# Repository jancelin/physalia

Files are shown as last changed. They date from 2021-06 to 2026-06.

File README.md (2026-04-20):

# PHYSALIA

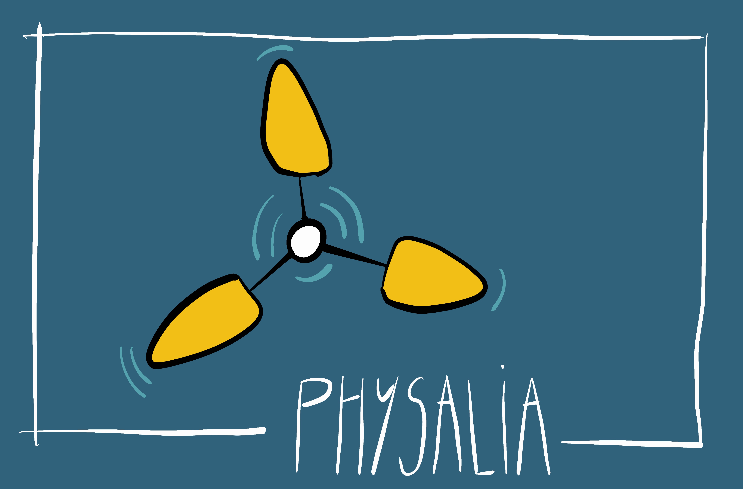
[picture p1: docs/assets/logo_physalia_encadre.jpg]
Physalia


## Plateforme HYdrographique pour la Surveillance Altimétrique du LIttoral

La surveillance du niveau de la mer et des niveaux hydrauliques des marais est un enjeu majeur dans la compréhension des dynamiques côtières et hydrologiques. Plusieurs études ont montré l’efficacité des bouées GNSS appliquées à la mesure du niveau de la mer. Toutefois, leur usage est généralement limité par le coût élevé d’un tel dispositif.

Plusieurs prototypes de bouées GNSS-RTK ont été développés afin de répondre à des problématiques liées à la surveillance en temps réel des variations du niveau de la mer et des marais littoraux. La réalisation des bouées est caractérisée par un besoin de réduction importante des coûts pour les rendre accessibles à tous.
Les bouées ont été construites autour d’une structure centrale et sont équipées de trois flotteurs montés sur des bras en acier inoxydable. La réception des signaux GNSS est assurée par un récepteur tri-fréquences qui utilise les constellations GPS, GLONASS, Galileo et Beidou. Les corrections RTK sont obtenues par le réseau [CentipedeRTK](https://centipede-rtk.org/). La réception des correction et le transfert des données produites est assurée par une connexion LTE.

## Objectifs

L’objectif et de suivre en continue avec une précision centimétrique les niveaux d’eau sur différents sites expérimentaux en marais doux atlantiques.

partenaires

-------------------------------------------------------
# Versions

## Physalia V1 maritime

version1

## Physalita hydro Marais

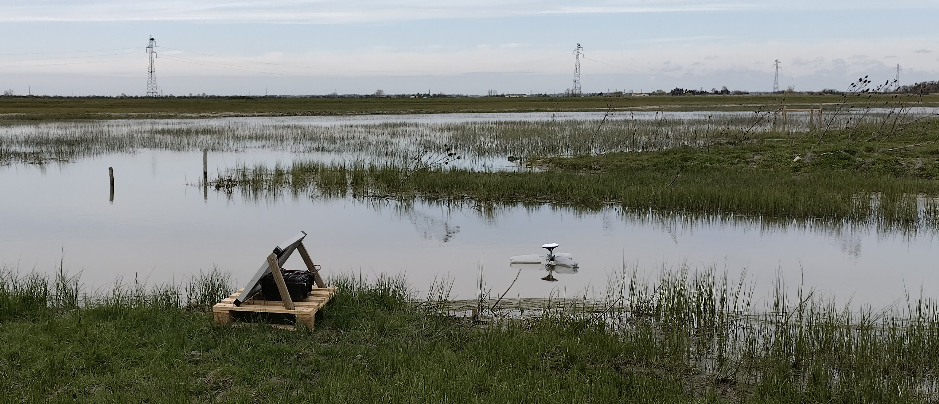
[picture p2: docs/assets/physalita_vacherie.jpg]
version_physalita


## Physalia V2 en développement

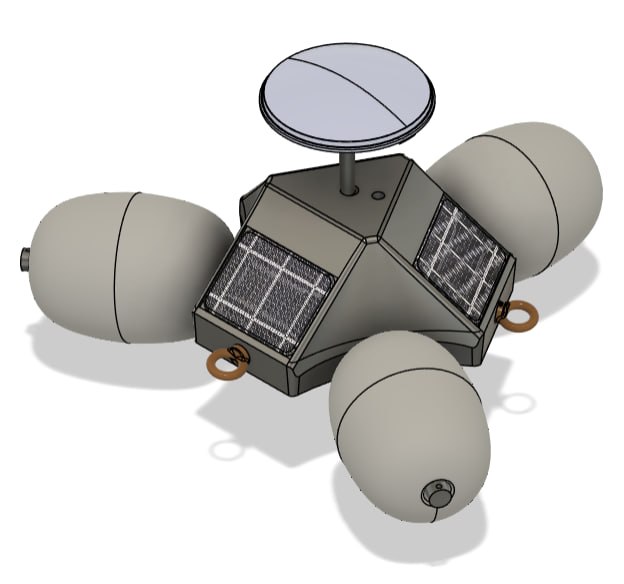
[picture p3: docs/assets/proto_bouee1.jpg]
version2


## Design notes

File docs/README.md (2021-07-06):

---
layout: default
title: 404
nav_exclude: true
---

# PHYSALIA

Documentation de PHYSALIA

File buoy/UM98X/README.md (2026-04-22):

# CONFIGURATION UM980

* Avec le navigateur Chrome ou Edge ouvrir la page https://webserial.centipede.fr/index_advanced.html
* connecter en USB le ROVER
* cliquer sur *Connecter*
* Uploader le fichier de configuration *UM90.cfg*
* cliquer sur *Envoyer*

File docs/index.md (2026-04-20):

---
layout: default
title: PHYSALIA
nav_order: 1
has_children: true
---

# PHYSALIA

Physalia

## Plateforme HYdrographique pour la Surveillance Altimétrique du LIttoral

La surveillance du niveau de la mer et des niveaux hydrauliques des marais est un enjeu majeur dans la compréhension des dynamiques côtières et hydrologiques. Plusieurs études ont montré l’efficacité des bouées GNSS appliquées à la mesure du niveau de la mer. Toutefois, leur usage est généralement limité par le coût élevé d’un tel dispositif.

Plusieurs prototypes de bouées GNSS-RTK ont été développés afin de répondre à des problématiques liées à la surveillance en temps réel des variations du niveau de la mer et des marais littoraux. La réalisation des bouées est caractérisée par un besoin de réduction importante des coûts pour les rendre accessibles à tous.
Les bouées ont été construites autour d’une structure centrale et sont équipées de trois flotteurs montés sur des bras en acier inoxydable. La réception des signaux GNSS est assurée par un récepteur tri-fréquences qui utilise les constellations GPS, GLONASS, Galileo et Beidou. Les corrections RTK sont obtenues par le réseau de base, [CentipedeRTK](https://centipede-rtk.org/). La réception des correction et le transfert des données produites est assurée par une connexion LTE.

## Objectifs

L’objectif et de suivre en continue avec une précision centimétrique les niveaux d’eau sur différents sites expérimentaux en marais doux atlantiques.

partenaires

-------------------------------------------------------
# Versions

## Physalia V1 maritime

version1

## Physalita hydro Marais

version_physalita

## Physalia V2 en développement

version2

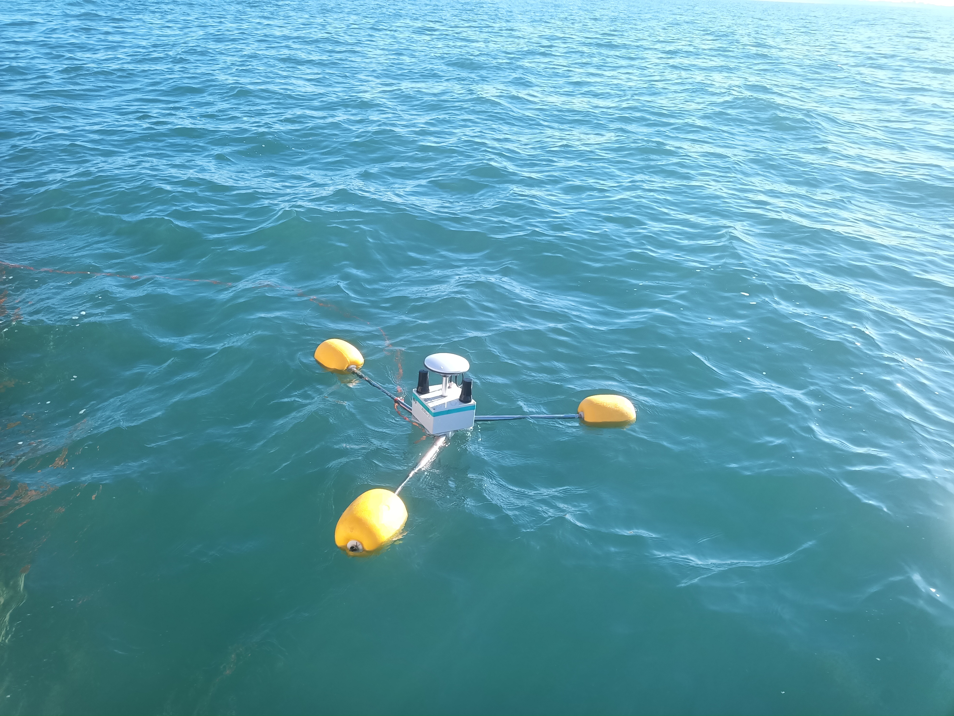
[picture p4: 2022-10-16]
docs/assets/thalia1_1022.jpg

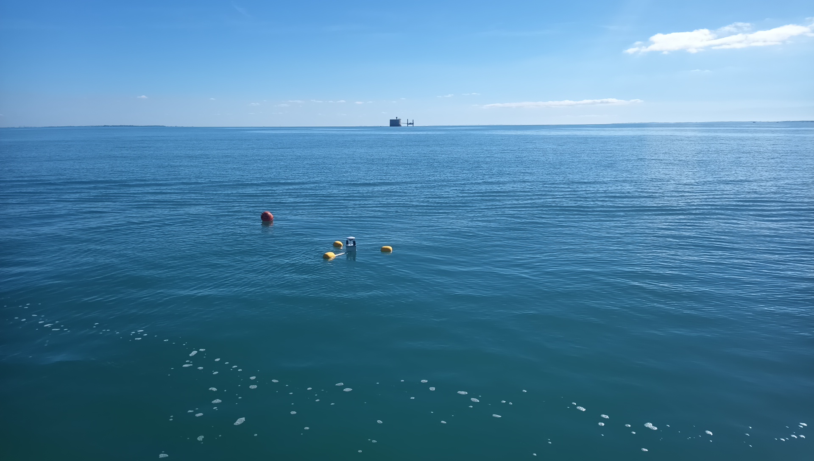
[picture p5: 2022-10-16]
docs/assets/thalia2_1022.jpg

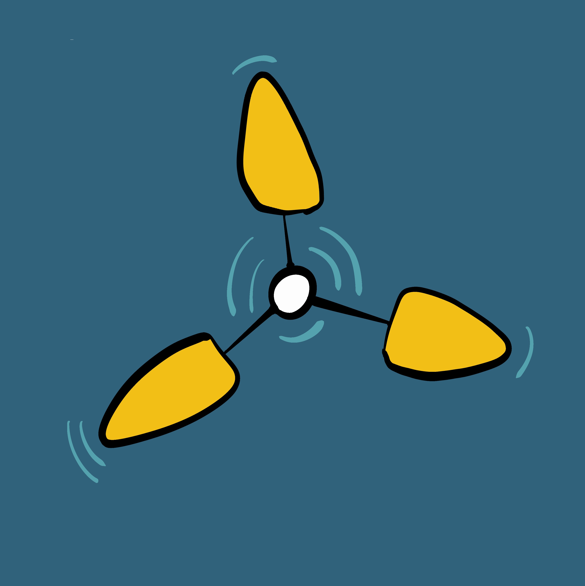
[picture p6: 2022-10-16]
docs/assets/logo.jpg

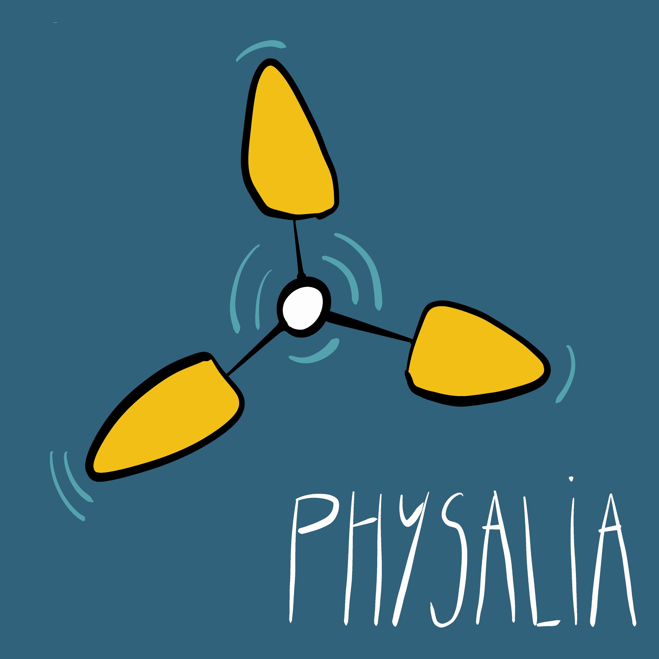
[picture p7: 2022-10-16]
docs/assets/logo_physalia.jpg

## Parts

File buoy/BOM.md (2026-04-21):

# BOM

## Elecronique

| composant | lien | Qte | prix unitaire HT |
| --- | --- | --- | --- |
| Mallette de transport Peli 1020 | https://fr.rs-online.com/web/p/mallettes-de-transport/0618786?gb=a | 1 | 31.4€ |
| Presse-étoupe HSK-K, M16 Hummel Gris, en Polyamide, IP68, Ø 4 mm à Ø 8 mm | https://fr.rs-online.com/web/p/presse-etoupes/0340144 | 1 | 0.44€ |
| diodes Schottky 1N5819 | https://fr.rs-online.com/web/p/diodes-schottky-et-de-redressements/4864460 | 3 | 0.94€ |
| Solar Panel 5V 200mA 110×80 mm | https://www.tinytronics.nl/en/power/solar-energy/solar-panels/solar-panel-5v-200ma-110x80mm | 3 | 3.5€ |
| Molicel 18650 Li-ion Battery - 3500mAh - 10A - INR18650-M35A | https://www.tinytronics.nl/en/power/batteries/18650/molicel-18650-li-ion-battery-3500mah-10a-inr18650-m35a | 1 | 4.13€ |
| LilyGO T-SIM7600G-H R2 - ESP32-WROVER - with 18650 Battery Holder | https://www.tinytronics.nl/en/development-boards/microcontroller-boards/with-telecommunication/lilygo-ttgo-t-sim7600g-h-r2-esp32-wrover-with-18650-battery-holder | 1 | 53.31€ |
| USB-C 2.0 Female to DIP Adapter | https://www.tinytronics.nl/en/cables-and-connectors/connectors/usb/usb-c-2.0-female-to-dip-adapter | 1 | 0.74€ |
| Pololu Mini interrupteur à glissière MOSFET avec protection contre les inversions de tension, LV | https://opencircuit.fr/produit/mini-mosfet-slide-switch-reverse-voltage | 1 | 3.4€ |
| UM980 Mic RTK GNSS receiver | https://gnss.store/products/elt0224 | 1 | 160€ |
| Budget All-band high precision GNSS antenna | https://gnss.store/products/elt0323 | 1 | 130€ |
| IP65 IPEX (U.FL) to SMA cable lenght 100mm panel thickness 8mm | http://gnss.store/products/elt0179?variant=55851776344396 | 1 | 6€ |
| Cordon sur mesure en coax faible perte UltraFlex LMR-240-UF 2.4/5 GHz (Ø 6.1mm) SMA mâle > TNC mâle 30 cm (sur demande) | http://mhzshop.com/Cables-et-cordons/Sur-mesure/50-ohms-WiFi-4G/Cordon-sur-mesure-en-coax-faible-perte-UltraFlex-LMR-240-UF-2-4-5-GHz-O-6-1mm.html | 1 | 19.6€ |
| total |  | | 422.34€| 
| Adafruit Ensemble de bobines de fil de raccordement - noyau solide 22AWG - 6 x 25 pi | https://opencircuit.fr/produit/hook-up-wire-spool-set-22awg-solid-core-6-x-25 | 1 | 21.6€ |
|  |  | | | 
| total |  | | 444€| 

## Structure

| matériel | lien | Qte | prix unitaire HT |
| --- | --- | --- | --- |
| Flotteur PB600 630g flottabilité 97x150mm  trou de 20mm Ø  | https://engelnetze.com/fr/flotteur-pb600-630g-flottabilite-97x150mm-trou-de-20mm/ | 3 | 6.2€ |  !
| tube inox ou fibre de verre |  | | |  
| platine assemblage |  | | |  
| Beitian RTK GNSS Base d'antenne GPS BT-M110SLB 18cm | https://fr.aliexpress.com/item/1005008470759973.html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 | 1 | 24.4€ |  
| tige d'extension de connexion GPS RTK en Fiber de carbone noire, mesure d'arpentage, diamètre 32mm, 10cm | https://fr.aliexpress.com/item/1005008788295319.html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 | 1 | 4.69€ |

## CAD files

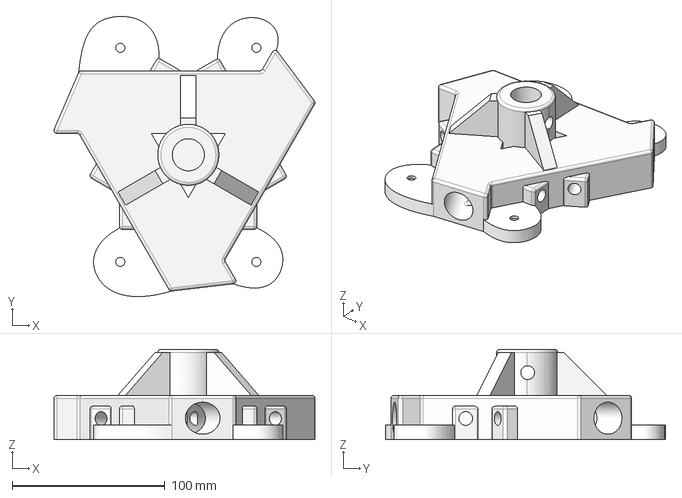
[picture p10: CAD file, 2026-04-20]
buoy/Printed-Parts/STEP/plan_corp_v1_8_4-Fusion041.step
170.7 x 183.3 x 59.0 mm

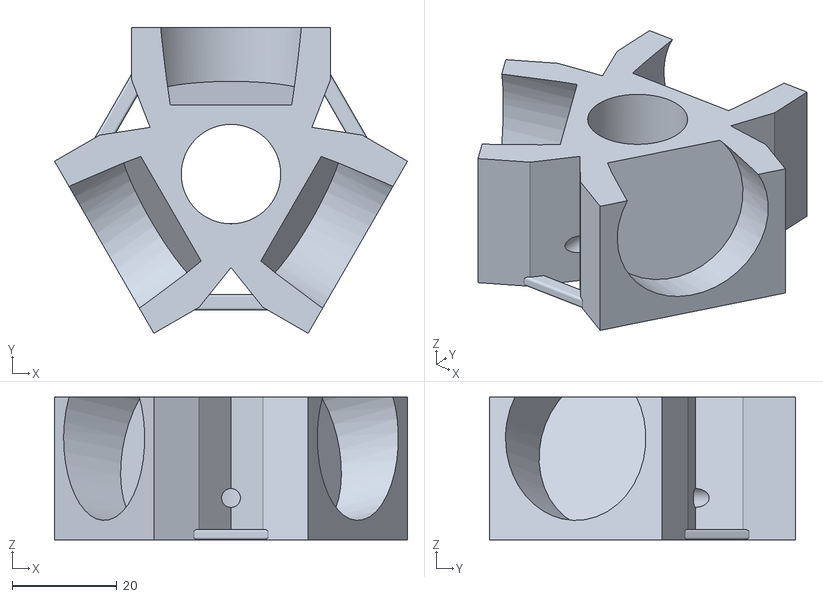
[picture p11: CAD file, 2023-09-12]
buoy/Printed-Parts/STL/physalita_5.stl
67.5 x 58.5 x 27.3

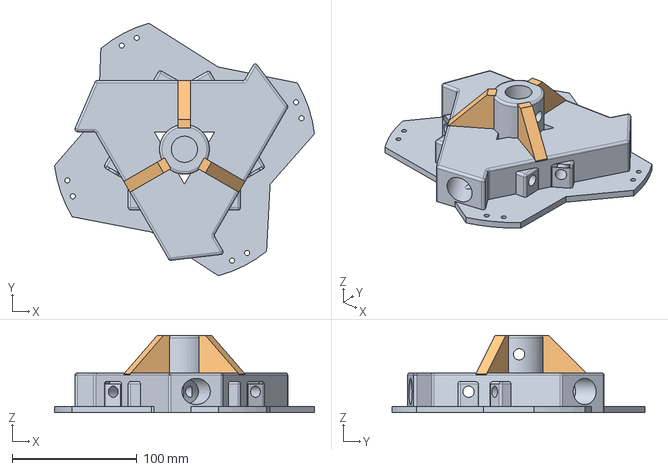
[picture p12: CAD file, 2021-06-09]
buoy/Printed-Parts/STEP/physalia_v1_7.step
208.4 x 202.5 x 62.0 mm

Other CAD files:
buoy/Printed-Parts/STL/physalia_v1_7.stl
buoy/Printed-Parts/STL/plan_corp_v1_8_4-Fusion041.stl
buoy/Printed-Parts/plan_corp_v1_8_4-Fusion041.3mf

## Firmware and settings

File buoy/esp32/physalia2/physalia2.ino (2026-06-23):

/*
=============================================================================================
PHYSALIA2 - UM980 edition
  - LTE NTRIP rover over SIM7600 (T-SIM7600G-H R2)
  - GNSS telemetry over MQTT
  - RTK fix via réseau Centipède-RTK (NTRIP)

Version énergie / mesure scientifique :
  Core 0 : gnssTask – lit l'UM980 en continu et pousse les PVTSLNA dans une queue courte.
  Core 1 : loop     – LTE/NTRIP/RTCM, stockage local des positions, publication MQTT groupée.
  
  Structure des fichiers :
  physalia2_dualcore.ino  – globals, setup(), loop(), gnssTask()
  ph_config.h             – pins, macros log, includes communs
  ph_globals.h            – struct PvtslnData + extern des globals
  ph_watchdog.cpp         – TWDT, failure handling, safeDeepSleep, BT off
  ph_modem.cpp            – setupGsm, maintainNetwork, modem_on/off, reset périodique
  ph_gnss.cpp             – processGnssSerial, parsePvtslnLine, setupGnss
  ph_ntrip.cpp            – maintainNtrip, processNtripStream, sendPeriodicGGA
  ph_mqtt.cpp             – publishFix, reconnect, callback, mapPositionType
  ph_battery.cpp          – ADC, readVbatMv, publishBatteryIfDue, publishPreSleepVbat
  ph_sleep.cpp            – setupDeepSleep, print_wakeup_reason
  secrets.h               – identifiants, paramètres réseau/timing
  secrets.cpp             – définitions uniques des variables globales
  NTRIPClient.h/.cpp      – librairie NTRIP
=============================================================================================
*/

#include "ph_config.h"
#include "ph_globals.h"
#include "secrets.h"

// =============================================================================
// DÉFINITIONS des objets et variables globales (extern déclarés dans ph_globals.h)
// =============================================================================

#ifdef DUMP_AT_COMMANDS
  #include <StreamDebugger.h>
  StreamDebugger _dbg(Serial1, Serial);
  TinyGsm        modem(_dbg);
#else
  TinyGsm        modem(Serial1);
#endif

TinyGsmClient  mqttTransport(modem, 0);
TinyGsmClient  ntripTransport(modem, 2);
PubSubClient   mqtt(mqttTransport);
NTRIPClient    ntripClient(ntripTransport);
HardwareSerial GNSSSerial(2);

// --- Timing / état cycle ---
unsigned long bootStarted_ms      = 0;
unsigned long lastReconnectAttempt = 0;
unsigned long lastReceivedRTCM_ms  = 0;
unsigned long lastGgaToCaster_ms   = 0;
unsigned long lastPvtsln_ms        = 0;
unsigned long lastState            = 0;   // alias historique : début de fenêtre utile RTK FIX
unsigned long firstGga_ms          = 0;
unsigned long lastNtripAttempt_ms  = 0;
unsigned long ntripConnected_ms    = 0;
unsigned long firstRtcm_ms         = 0;
unsigned long firstFloat_ms        = 0;
unsigned long firstFix_ms          = 0;
unsigned long rtkFixStart_ms       = 0;
bool ggaSentToCaster               = false;
bool cycleClosed                   = false;

// --- Buffer UART GNSS ---
char   gnssLine[GNSS_LINE_BUFFER_SIZE];
size_t gnssLineLen = 0;
String lastGGASentence;

// --- Dernier fix PVTSLNA + batch de positions du cycle ---
PvtslnData lastFix;
PvtslnData fixBatch[PH_FIX_BATCH_MAX_RECORDS];
uint16_t fixBatchCount = 0;
uint32_t fixBatchDropped = 0;
uint16_t fixBatchHead    = 0;   // [P6]
uint16_t fixBatchTail    = 0;   // [P6]

// --- Batterie : batch local publié en fin de cycle ---
BatterySample batterySamples[PH_BATTERY_BATCH_MAX_RECORDS];
uint8_t batterySampleCount = 0;

// --- FreeRTOS ---
QueueHandle_t     pvtQueue  = nullptr;
SemaphoreHandle_t ggaMutex  = nullptr;

// --- Watchdog ---
bool taskWdtEnabled = false;

// --- RTC RAM (persist à travers deep-sleep) ---
RTC_DATA_ATTR uint32_t bootCount              = 0;
RTC_DATA_ATTR uint8_t  consecutiveFailureCount= 0;
RTC_DATA_ATTR uint32_t cyclesSinceModemReset  = 0;
RTC_DATA_ATTR uint8_t  failureSleepCount      = 0;
RTC_DATA_ATTR bool     lastBootWasRestart     = false;
RTC_DATA_ATTR uint32_t lastRestartTimestampMs = 0;
RTC_DATA_ATTR uint32_t cycleId                = 0;

// --- Batterie ---
int    vref         = 1100;
uint32_t timeStamp  = 0;
esp_adc_cal_characteristics_t adcChars;
bool   adcCalibrated = false;
RTC_DATA_ATTR int32_t rtcVbatMinMv   = 9999;
RTC_DATA_ATTR int32_t rtcVbatEmaMv   = 0;
RTC_DATA_ATTR bool    rtcVbatEmaInit = false;

// =============================================================================
// PROTOTYPES
// =============================================================================
void disableUnusedBluetooth();
void setupTaskWatchdog();
void registerCurrentTaskToWatchdog(const char *name);
void feedTaskWatchdog();
void resetFailureCycleCounter(const char *reason);
void handleFailureCycleAndSleep(const char *stage);
void safeDeepSleep();
void periodicModemHardReset();
void setupGsm();
void maintainNetwork();
void modem_on();
void modemPowerStartEarly();
void modem_off();
void setupGnss();
void processGnssSerial();
void processGnssLine(const char *line);
bool parsePvtslnLine(const char *line, PvtslnData &out);
void maintainNtrip();
void processNtripStream();
void sendPeriodicGGA();
void publishFix(const PvtslnData &fix);
boolean reconnect();
void callback(char *topic, byte *payload, unsigned int length);
void setupBatteryCalibration();
int32_t readVbatMv();
void publishBatteryIfDue(const char *dt);
void publishPreSleepVbat();
void recordBatterySample(const char *stage, const char *datetimeValue = nullptr);
void setupDeepSleep();
void print_wakeup_reason();
void appendFixSample(const PvtslnData &fix);
bool isRtkFixedType(const char *type);  // [P1] char* — ph_cycle.cpp
bool isRtkFloatType(const char *type);  // [P1] char* — ph_cycle.cpp
bool publishCycleAndStatus(const char *status);
void gnssTask(void *param);
void drainPvtQueueToBatch();
void powerOffGnssAfterAcquisition();

// =============================================================================
// SETUP
// =============================================================================
void setup()
{
  bootStarted_ms = millis();
  cycleId++;
  Serial.begin(115200);
  LOGLN(1, "********************************");
  LOGLN(1, "***** PHYSALIA2 UM980 SETUP ****");
  LOGLN(1, "********************************");
  LOGF(1, "Cycle id=%lu\n", (unsigned long)cycleId);

  setupTaskWatchdog();

  // Protection boucle de restart rapide
  {
    const uint32_t nowMs = (uint32_t)millis();
    if (lastBootWasRestart && lastRestartTimestampMs > 0) {
      // [FIX Bug2] Après ESP.restart(), millis() repart de 0.
      // La soustraction uint32 (0 - 25000) = 4 294 942 396 → jamais < 30000.
      // On détecte ce cas : si nowMs < lastRestartTimestampMs, on est
      // nécessairement dans les premières secondes après restart.
      const bool withinWindow =
          (nowMs < lastRestartTimestampMs) ||
          ((nowMs - lastRestartTimestampMs) < 30000UL);
      if (withinWindow) {
        LOGF(1, "Rapid restart loop detected (%lu ms) – forcing deep sleep\n",
             (unsigned long)lastRestartTimestampMs);
        lastBootWasRestart      = false;
        consecutiveFailureCount = 0;
        // Coupure hardware modem OBLIGATOIRE avant sleep.
        // AT non disponible (modem non init), on coupe directement PWR_PIN.
        // Sans ça, le SIM7600 reste alimenté, perturbe modemPowerStartEarly()
        // au réveil suivant et verrouille le système en boucle infinie.
        pinMode(PWR_PIN, OUTPUT);
        digitalWrite(PWR_PIN, LOW);
        delay(1600);                // > 1.5s = power-off garanti (spec SIM7600)
        digitalWrite(PWR_PIN, HIGH);
        delay(300);
        esp_sleep_enable_timer_wakeup((uint64_t)TIME_TO_SLEEP * uS_TO_S_FACTOR);
        esp_deep_sleep_start();
      }
    }
    lastBootWasRestart = false;
  }

  // Alimentation GNSS immédiate : le temps UM980 se superpose au délai LTE.
  pinMode(PIN_GNSS_EN, OUTPUT);
  digitalWrite(PIN_GNSS_EN, HIGH);
  delay(200);

  // Démarrage LTE le plus tôt possible, sans modifier le reste du cycle validé.
  // La séquence SIM7600 démarre pendant que le setup prépare RTOS/GNSS/batterie.
  periodicModemHardReset();
  modemPowerStartEarly();

  disableUnusedBluetooth();

  pvtQueue = xQueueCreate(PVT_QUEUE_DEPTH, sizeof(PvtslnData));
  ggaMutex = xSemaphoreCreateMutex();
  if (!pvtQueue || !ggaMutex) {
    Serial.println("FATAL: RTOS alloc failed – restarting");
    feedTaskWatchdog();
    lastBootWasRestart     = true;
    lastRestartTimestampMs = (uint32_t)millis();
    ESP.restart();
  }

  print_wakeup_reason();
  setupDeepSleep();
  setupBatteryCalibration();
  recordBatterySample("boot", nullptr);

  // UM980 d'abord, puis tâche Core 0 avant la 4G : acquisition GGA/PVTSLNA en parallèle du LTE.
  setupGnss();
  xTaskCreatePinnedToCore(gnssTask, "gnssTask", 4096, nullptr, 2, nullptr, 0);
  LOGLN(1, "GNSS task started on Core 0");

  setupGsm();
  recordBatterySample("lte", nullptr);

  // MQTT est configuré ici mais connecté uniquement après l'acquisition.
  mqtt.setServer(mqttServer, mqttPort);
  mqtt.setBufferSize(MQTT_BUFFER_SIZE);
  mqtt.setCallback(callback);

  while (Serial.available()) Serial.read();
}

// =============================================================================
// LOOP  (Core 1 – réseau + automate de cycle)
// =============================================================================
void loop()
{
  static unsigned long lastContinuousPublish_ms = 0;
  feedTaskWatchdog();
  unsigned long now = millis();

  // Vide la queue PVT produite par gnssTask (Core 0) dans le batch local.
  drainPvtQueueToBatch();
  maintainNetwork();
  maintainNtrip();
  processNtripStream();
  sendPeriodicGGA();

  now = millis();

  // MQTT n'est utilisé qu'après acquisition ; si déjà connecté, maintenir la session.
  if (mqtt.connected()) mqtt.loop();

  // PATCH mode continu : publication périodique toutes les 5s
  // Actif uniquement quand DEEP_SLEEP_ACTIVATED = false
  if (!DEEP_SLEEP_ACTIVATED
      && fixBatchCount >= PH_GEO_BATCH_CHUNK_RECORDS
      && millis() - lastContinuousPublish_ms >= 5000UL) {
    if (!mqtt.connected()) reconnect();
    cycleClosed = false; // reset le verrou one-shot avant chaque publish continu
    publishCycleAndStatus("continuous");
    lastContinuousPublish_ms = millis();
    fixBatchCount = 0;   // repart à zéro pour le prochain bloc
    fixBatchHead  = 0;   // patch P6
    fixBatchTail  = 0;   // patch P6
    batterySampleCount = 0; // évite la re-publication des mêmes samples batterie
  }

  // Sécurité : si l'UM980 ne produit pas de GGA exploitable assez vite.
  if (DEEP_SLEEP_ACTIVATED && firstGga_ms == 0 &&
      now - bootStarted_ms > NO_GGA_TIMEOUT_MS) {
    LOGLN(1, "No GGA within energy budget – publish diagnostic and sleep");
    publishPreSleepVbat();
    publishCycleAndStatus("no_gga");
    safeDeepSleep();
  }

  // Si le caster est connecté mais aucun RTCM n'arrive rapidement.
  if (DEEP_SLEEP_ACTIVATED && ntripConnected_ms != 0 && firstRtcm_ms == 0 &&
      now - ntripConnected_ms > NO_RTCM_TIMEOUT_MS) {
    LOGLN(1, "No RTCM after NTRIP connect – publish diagnostic and sleep");
    publishPreSleepVbat();
    publishCycleAndStatus("no_rtcm");
    safeDeepSleep();
  }

  // Si les corrections arrivent mais qu'aucun RTK FIX n'est obtenu dans le budget.
  if (DEEP_SLEEP_ACTIVATED && ntripConnected_ms != 0 && rtkFixStart_ms == 0 &&
      now - ntripConnected_ms > (unsigned long)RTK_MAX_RESEARCH * 1000UL) {
    LOGLN(1, "RTK FIX not reached within search budget – publish all positions and sleep");
    publishPreSleepVbat();
    publishCycleAndStatus("no_fix");
    safeDeepSleep();
  }

  // Fin nominale : 5 s d acquisition utile après premier RTK FIX.
  if (DEEP_SLEEP_ACTIVATED && rtkFixStart_ms != 0 &&
      now - rtkFixStart_ms > (unsigned long)RTK_ACQUISITION_PERIOD * 1000UL) {
    LOGLN(1, "RTK FIX record period done - GNSS off, publish batch and deep sleep");

    // Dernière vidange de la queue avant coupure UM980 : les positions sont déjà en RAM.
    drainPvtQueueToBatch();
    feedTaskWatchdog();
    delay(25);
    drainPvtQueueToBatch();

    // À partir d ici, l acquisition est terminée : on économise l UM980 pendant MQTT.
    powerOffGnssAfterAcquisition();

    failureSleepCount       = 0;
    consecutiveFailureCount = 0;
    publishPreSleepVbat();
    publishCycleAndStatus("ok_fix");
    safeDeepSleep();
  }

  feedTaskWatchdog();
  delay(5);
}

// =============================================================================
// =============================================================================
// ACQUISITION HELPERS
// =============================================================================
void drainPvtQueueToBatch()
{
  if (!pvtQueue) return;

  PvtslnData fix;
  while (xQueueReceive(pvtQueue, &fix, 0) == pdTRUE) {
    appendFixSample(fix);
    publishBatteryIfDue(fix.datetime);  // échantillonne localement, ne publie pas encore
  }
}

void powerOffGnssAfterAcquisition()
{
  static bool gnssOffAfterAcq = false;
  if (gnssOffAfterAcq) return;
  gnssOffAfterAcq = true;

  // Le flux RTCM n est plus utile après la fenêtre de mesure.
  if (ntripClient.connected()) {
    ntripClient.stop();
    LOGLN(1, "NTRIP stopped after acquisition");
  }

  GNSSSerial.flush();
  pinMode(PIN_GNSS_EN, OUTPUT);
  digitalWrite(PIN_GNSS_EN, LOW);
  LOGF(1, "UM980 powered off after acquisition at %lu ms\n",
       (unsigned long)(millis() - bootStarted_ms));
}

// GNSS TASK  (Core 0 – lecture UART uniquement, jamais de réseau)
// =============================================================================
void gnssTask(void *param)
{
  (void)param;
  registerCurrentTaskToWatchdog("gnssTask");
  for (;;) {
    processGnssSerial();
    feedTaskWatchdog();
    vTaskDelay(pdMS_TO_TICKS(1));
  }
}

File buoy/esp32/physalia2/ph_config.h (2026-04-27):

#pragma once
// =============================================================================
// ph_config.h – Configuration matérielle, macros de log, dépendances globales
// =============================================================================
// Ce fichier est inclus en PREMIER dans tous les .cpp et dans le .ino.
// Les #define TinyGSM DOIVENT précéder #include <TinyGsmClient.h>.
// =============================================================================

#include <Arduino.h>
#include <SPI.h>
#include <esp_adc_cal.h>
#include <ArduinoJson.h>
#include <PubSubClient.h>
#include <time.h>
#include <esp_task_wdt.h>
#include <freertos/FreeRTOS.h>
#include <freertos/queue.h>
#include <freertos/semphr.h>

// Bluetooth (désactivé en production)
#if defined(ARDUINO_ARCH_ESP32) && __has_include("esp32-hal-bt.h")
  #include "esp32-hal-bt.h"
#endif

// -------------------------------------------------------------------------------------------------
// TinyGSM – doit être défini AVANT l'include
// -------------------------------------------------------------------------------------------------
#define TINY_GSM_RX_BUFFER 1024
#define TINY_GSM_MODEM_SIM7600
#define TINY_GSM_DEBUG Serial
#define TINY_GSM_USE_GPRS true
#define TINY_GSM_USE_WIFI false
#include <TinyGsmClient.h>

// -------------------------------------------------------------------------------------------------
// Log macros  (LOG_LEVEL défini dans secrets.h : 0=rien, 1=minimal, 2=complet)
// -------------------------------------------------------------------------------------------------
#define LOGLN(lvl, msg)      do { if (LOG_LEVEL >= (lvl)) Serial.println(msg); } while(0)
#define LOG(lvl, msg)        do { if (LOG_LEVEL >= (lvl)) Serial.print(msg);   } while(0)
#define LOGF(lvl, fmt, ...)  do { if (LOG_LEVEL >= (lvl)) Serial.printf(fmt, ##__VA_ARGS__); } while(0)
#define LOGBLOCK(lvl)        if (LOG_LEVEL >= (lvl))

// -------------------------------------------------------------------------------------------------
// Mapping matériel – T-SIM7600G-H R2
// -------------------------------------------------------------------------------------------------

// GNSS (UM980 via Pololu 2810)
#define PIN_GNSS_EN  23
#define UM980_TX_PIN 22   // ESP32 TX → UM980 RXD2
#define UM980_RX_PIN 21   // ESP32 RX ← UM980 TXD2
#define UM980_BAUD   460800

// SIM7600 UART + contrôle alimentation
#define UART_BAUD 115200
#define PIN_TX    27
#define PIN_RX    26
#define PWR_PIN   4       // PWRKEY SIM7600 (hold LOW >1.5s = power-off)
#define LED_PIN   12
#define POWER_PIN 25      // DC-DC boost enable
#define IND_PIN   36
#define SerialAT  Serial1 // UART modem SIM7600

// ADC batterie – T-SIM7600G-H R2 : 18650 → diviseur 100kΩ/100kΩ → GPIO35 (ADC1_CH7)
// GPIO4 = PWR_PIN numérique → ne PEUT PAS être ADC simultanément.
// AT+CBC lit la tension régulée du modem (~4.1V fixe), inutile pour surveiller la décharge.
#define ADC_PIN 35

// -------------------------------------------------------------------------------------------------
// Constantes runtime figées
// -------------------------------------------------------------------------------------------------
static const uint32_t TASK_WDT_TIMEOUT_S      = 60;
static const uint8_t  FAILURE_REBOOT_THRESHOLD = 3;
static const size_t   GNSS_LINE_BUFFER_SIZE    = 1024;
static const uint16_t PVT_QUEUE_DEPTH          = 240;  // 48 s à 5 Hz pendant setupGsm() bloquant
static const unsigned long MAX_HANGUP_MS       = 10000UL;

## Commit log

2021-06-09 Squashed 'buoy/RTKrover/' content from commit 9026f47
    git-subtree-dir: buoy/RTKrover
    git-subtree-split: 9026f472d94e4ff8be77c0181eeeafaaead6d2b2
    [U-Blox_ZED-F9P_config_info.txt, U-Blox_ZED-F9P_rtkbase.cfg, fond de panier rtkbase.FCStd]
2021-06-09 rm subtree
    [U-Blox_ZED-F9P_config_info.txt, U-Blox_ZED-F9P_rtkbase.cfg, fond de panier rtkbase.FCStd]
2021-06-09 add printed parts
    [physalia_v1_7.step, physalia_v1_7.stl]
2021-07-06 upd docs
    [materiel.csv, materiel.ods]
2022-03-09 esp32 gnss
2022-03-09 esp32 gnss mqtt connexion
2022-03-09 esp32 gnss mqtt OK!
2022-03-09 esp32 gnss normalise date time
2022-03-09 esp32 add generic secrets.h
2022-03-11 Add Mac adresse to material id
2022-03-11 esp32 auto reconnect wifi
2022-03-11 esp32 send gga on/off move option to secrets.h
2022-03-11 upd material id for combine with Mac address
2022-03-21 SIM800 integration+ change GNSS I2C 18-19
2023-09-12 upd mavi
    [physalita_5.stl]
2023-09-12 upd buoy_mavi stl
    [physalita_5.stl]
2023-09-13 Renamed .ino file to match dir name (required by Arduino)
2023-09-19 Added assembly documentation and did some changes
2023-09-21 Updated assembly documentation
2023-10-27 MAVI: upd 3d, f9p conf, libraries, + resolve bug ntrip ino
    [physalita_5.stl]
2023-12-12 Adding relay control for GNSS & GSM
2023-12-29 Adding Lux sensor SEN0562 data
2024-02-02 Adding control for reboot
    [secrets.h]
2024-02-02 modify battery_voltage + add variable GNSS_FREQ
2024-02-13 deplacement void gnss en fin de programme
2024-02-15 upd arduino json librairies
2024-03-14 ADDING Reboot after nb_count deepsleep
    [secrets.h]
2026-04-02 new code 4 new buoy physalia2. add dual core esp32
2026-04-02 Démarrer lastState au moment de la connexion NTRIP, pas dans loop(): 20s d'acquisition
2026-04-20 cleaning for update to physalia2
    [materiel.csv, materiel.ods, physalita_5.stl]
2026-04-20 add files for update to physalia2
    [physalita_5.stl, plan_corp_v1_8_4-Fusion041.3mf, plan_corp_v1_8_4-Fusion041.step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]
2026-04-21 add BOM
2026-04-22 config GNSS
    [UM980.cfg]
2026-04-27 optimisation data send et structuredata: le cycle actif passe d’environ 50 s à 35,9 s, soit environ 14 s économisées par cycle
2026-05-02 Patchs P1 (String→char[]) et C3 (delay): Fiabilité H24 long terme
2026-05-05 patch firmware hang SIM7600G-H,: le modem est sous tension mais ne répond plus aux commandes
2026-05-07 patch de fonctionnement du deepslepp false (acquisition continue)
2026-05-07 patch P6 — Buffer circulaire
2026-05-11 deepsleep false: reset le verrou one-shot avant chaque publish continu > maintenant fonctionne
    [physalia2.ino]
2026-06-22 correction du dépassement uint32
    [physalia2.ino]
2026-06-22 corrige 2 bugs sur les 2 derniers commits
    [ph_modem.cpp, physalia2.ino]
2026-06-23 patch void safeDeepSleep(); et sortie directe après hard reset dans maintainNetwork()
    [ph_modem.cpp, physalia2.ino]
